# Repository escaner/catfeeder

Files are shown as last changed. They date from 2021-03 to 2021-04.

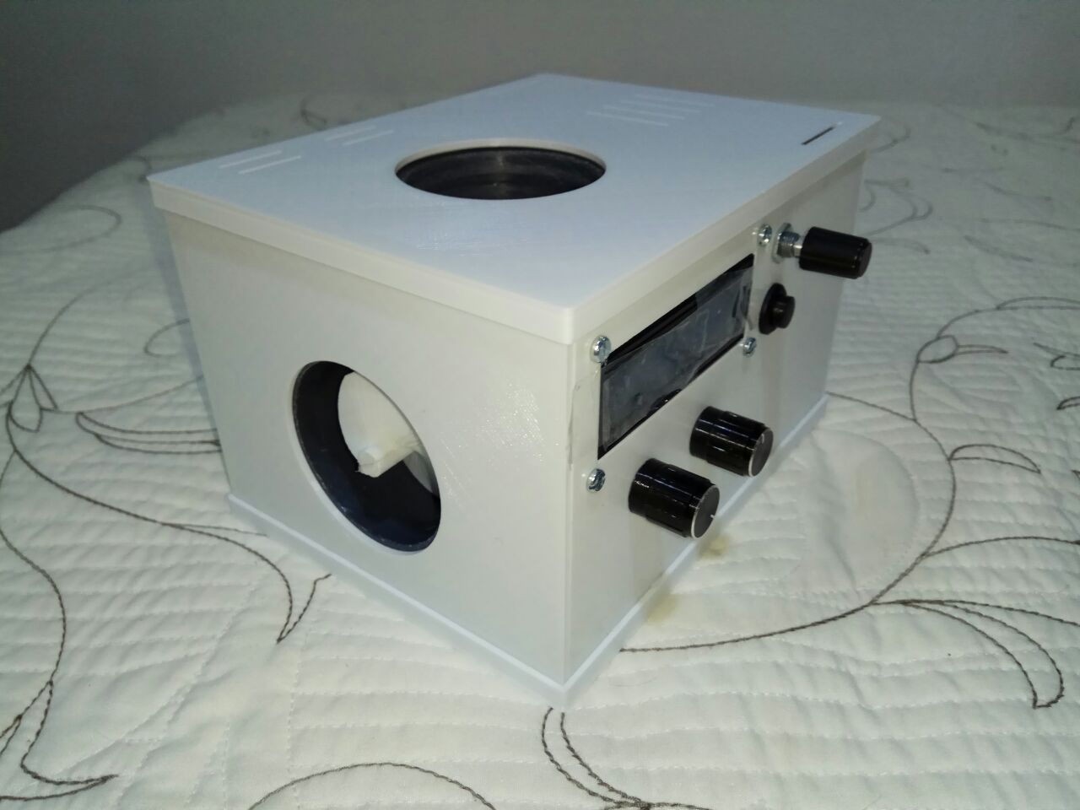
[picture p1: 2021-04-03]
doc/images/case2.jpg

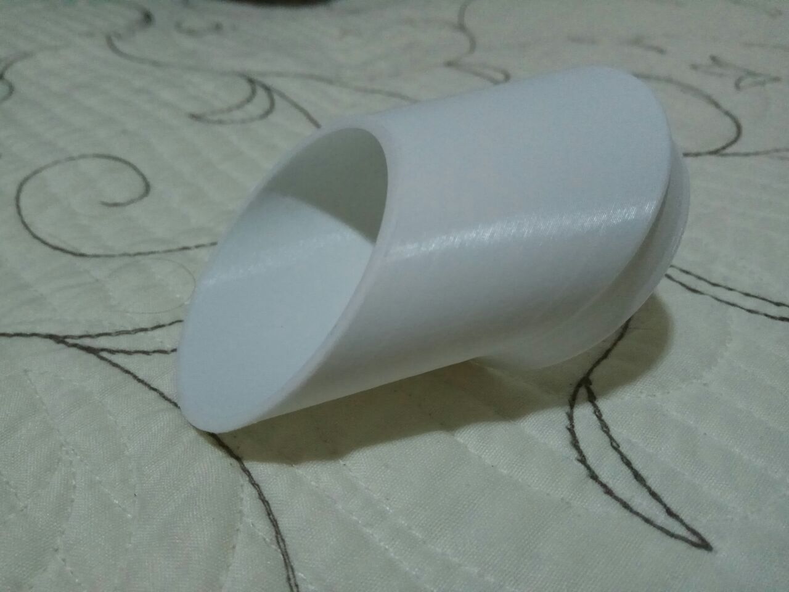
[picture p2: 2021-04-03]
doc/images/ramp1.jpg

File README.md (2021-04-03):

https://github.com/escaner/catfeeder

Catfeeder is an Arduino project to build am automatic cat feeder that
allows to program several feeding times so your mascot keeps getting food.

3D printed parts can be found here:
https://www.thingiverse.com/thing:4815584

The core of the system is an Arduino Nano or clone (small Arduino Uno
compatible) with a stepper motor connected to an auger, a display,
some buttons and a real time clock to keep the time in case the power
temporarily fails.

This is the list of electronic parts for the project:

* 1 x Arduino Nano compatible microcontroller
* 1 x SchmalzHaus EasyDriver: stepper motor controller
* 1 x Hanpose 17HS3430 stepper motor (12V)
* 1 x 1602 LCD display (without I2C module)
* 1 x Potentiometer 5 (or 10) KOhm for display brightness
* 1 x Potentiometer 10 KOhm for display contrast
* 1 x rotary encoder with pushbutton
* 1 x temporary pushbutton
* 1 x Robotdyn DS1307 I2C RTC module with battery as real time clock and backup
* 1 x Robotdyn LM2596 DC-DC Step-down Adjustable Power Supply Module (set
  to 5V output)
* 1 x DC barrel jack for 12V DC input required by the motor
* 1 x 12V 1.2A DC power supply (brick wall or as you prefer)

Note that in order for the reset function to correctly work, the Arduino Nano
needs to have the new Optiboot bootloader: the old one bugs out on reset
with the watchdog library.

More info can be found in the doc directory, including schematics and
pictures.

Other items used:
* 3D printer for case and parts
* Drill and 3mm bit to make hole in the T for the screw where the motor mount
  will lean
* PVC 50mm T pipe for water
* Epoxy two component glue (to fix T, bottom and front sides of case)
* Hot glue gun (to fix motor mount to T, left and right sides of case and
  also Arduino, motor controller and RTC to the case)
* M3 screws and nuts (to fix LCD, motor to its mount, auger to motor, screw in
  T and switched power supply)

Software features:
* Eight (can be increased up to 10) programmable feed times (including time,
  days of the week and quantity). Stored in the Arduino EEPROM (not lost on
  power off).
* Real Rime Clock with battery to keep time in case of power loss.
* Possibility of skipping next feed
* Time stored in UTC format for automatic DST changes (CET timezone
  programmed, can be easily changed in config.h).
* Day of the week is currently in Spanish, but not hard to change to English,
  code already prepared for that.
* Customizable through config.h and catfeeder.ino constants.
* Main display shows current date and time and also next feed day and time
* Manual feed function

This software needs my libraries REncoder and Switch:
https://github.com/escaner/REncoder
https://github.com/escaner/Switch

This project is based on Kitlaan and dodgey99 projects, seen here:
http://www.thingiverse.com/thing:27854
https://www.instructables.com/Automatic-Arduino-Powered-Pet-Feeder/

Copyright (C) 2020-2021, Óscar Laborda

This file is part of Catfeeder software.

Catfeeder is free software: you can redistribute it and/or modify
it under the terms of the GNU General Public License as published by
the Free Software Foundation, either version 3 of the License, or
(at your option) any later version.

Catfeeder is distributed in the hope that it will be useful,
but WITHOUT ANY WARRANTY; without even the implied warranty of
MERCHANTABILITY or FITNESS FOR A PARTICULAR PURPOSE.  See the
GNU General Public License for more details.

You should have received a copy of the GNU General Public License
along with Catfeeder.  If not, see <https://www.gnu.org/licenses/>.

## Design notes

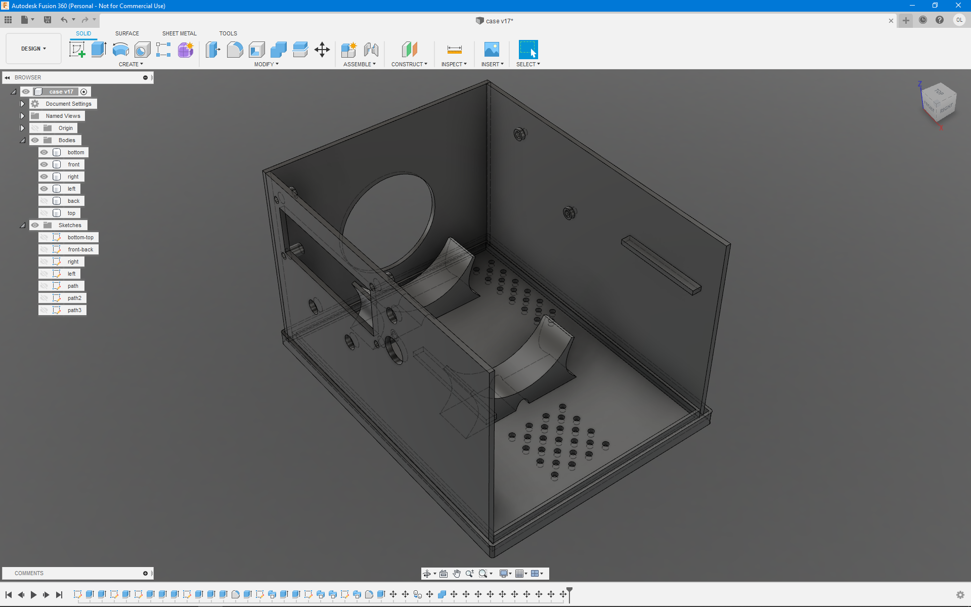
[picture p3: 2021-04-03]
doc/images/case6.png

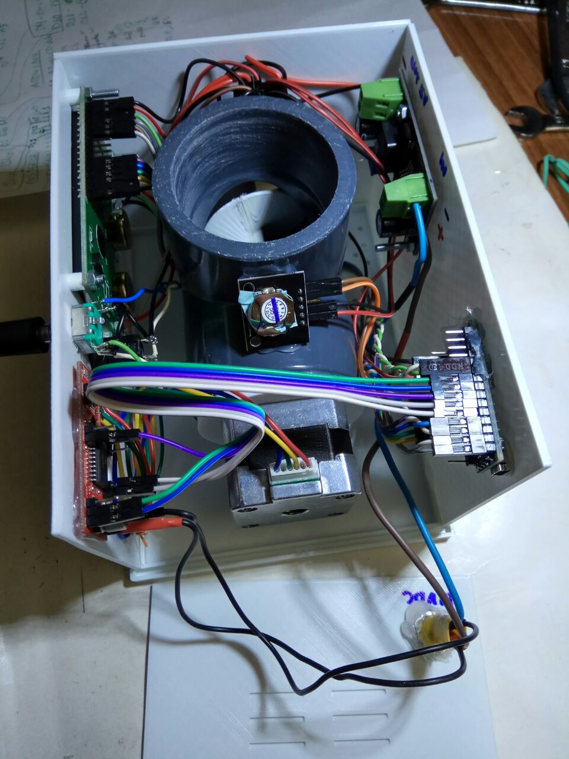
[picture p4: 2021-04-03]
doc/images/inside0.jpg

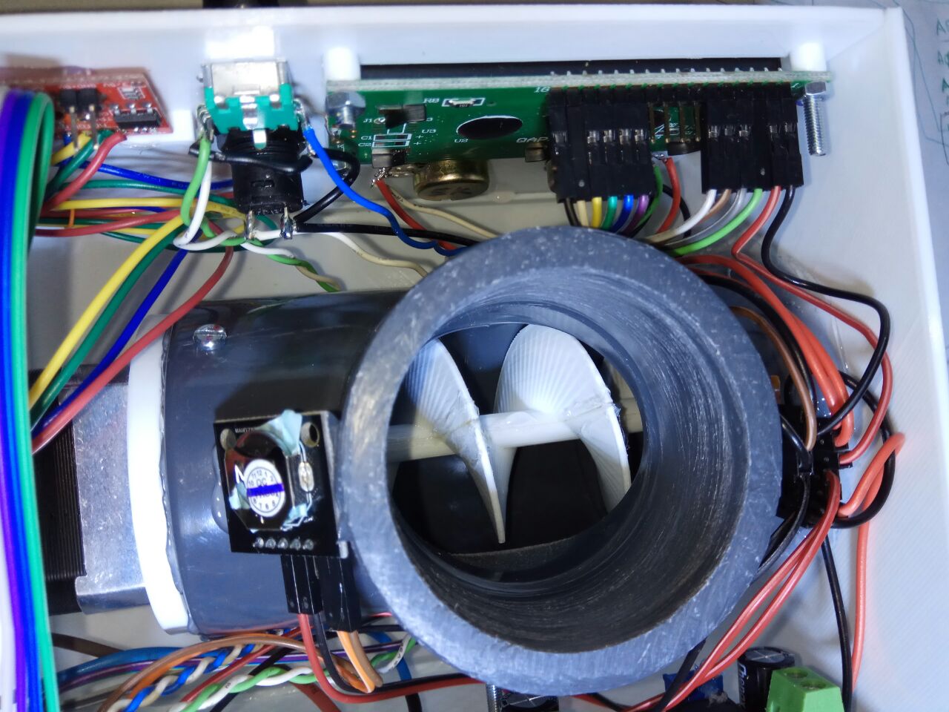
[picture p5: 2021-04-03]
doc/images/inside1.jpg

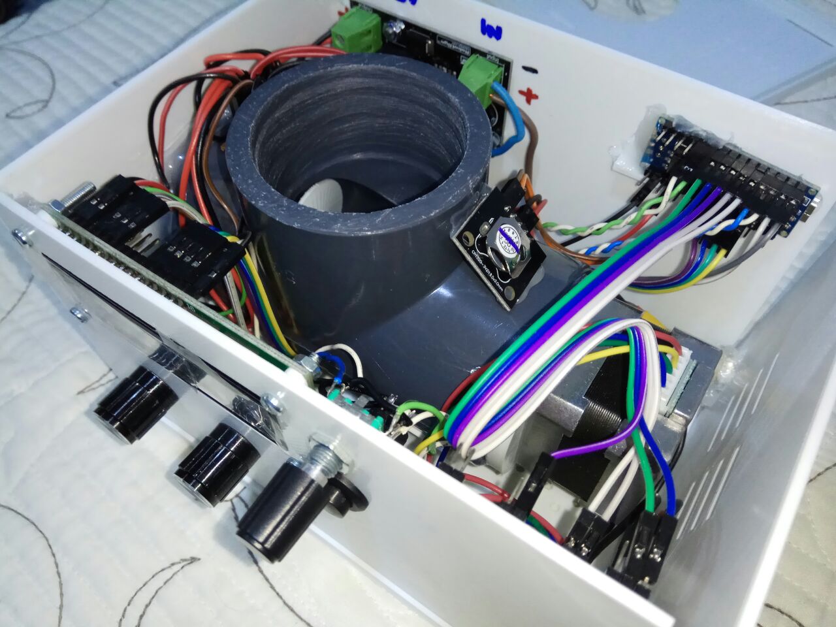
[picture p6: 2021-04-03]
doc/images/inside2.jpg

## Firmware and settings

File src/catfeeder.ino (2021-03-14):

#include "config.h"
#include <avr/wdt.h>
#include "event.h"
#include "action.h"
#include "feeds.h"
#include "switchpnl.h"
#include "clock.h"
#include "display.h"
#include "auger.h"


/*************/
/* Constants */
/*************/

// Swtich & encoder constants
static const uint8_t ENC_NUM_PINS = 2U;  // Number of pins per encoder
static const uint8_t NUM_BUTTONS = 2U;  // Number of swtiches of type button

// ARDUINO NANO connections
// Switches
static const uint8_t PIN_ENC[ENC_NUM_PINS] = { 2, 3 };
static const uint8_t PIN_BTN_ENT = 9;
static const uint8_t PIN_BTN_BCK = 10;
// Display
static const uint8_t PIN_LCD_RS = 12;
static const uint8_t PIN_LCD_E = 11;
static const uint8_t PIN_LCD_D4 = A3;
static const uint8_t PIN_LCD_D5 = A2;
static const uint8_t PIN_LCD_D6 = A1;
static const uint8_t PIN_LCD_D7 = A0;
// RTC
static const uint8_t PIN_RTC_SDA = A4;
static const uint8_t PIN_RTC_SCL = A5;
// EasyDriver with stepper motor
static const uint8_t PIN_ED_ENABLE = 8;
static const uint8_t PIN_ED_MS1 = 6;
static const uint8_t PIN_ED_MS2 = 7;
static const uint8_t PIN_ED_DIR = 5;
static const uint8_t PIN_ED_STEP = 4;


/*************/
/* Variables */
/*************/

// Object to control feeding times
static Feeds FeedData;

// Object to manage the input buttons and rotary encoder
static SwitchPnl SwitchPanel(PIN_ENC[0], PIN_ENC[1], PIN_BTN_ENT, PIN_BTN_BCK);

// Object to manage time and conversions
static Clock Rtc(TIMEZONE_DIFF, ENABLE_DST);

// Object to manage the LCD display
static Display Lcd(PIN_LCD_RS, PIN_LCD_E, PIN_LCD_D4, PIN_LCD_D5, PIN_LCD_D6,
  PIN_LCD_D7);

// Object to control the auger on the EasyDriver stepper motor
static Auger Edsm(PIN_ED_STEP, PIN_ED_DIR, PIN_ED_MS1, PIN_ED_MS2,
  PIN_ED_ENABLE, AUGER_RPM, AUGER_EIGHTH_REVS_PER_MEAL_QTY,
  AUGER_EIGHTH_REVS_BACKUP);


/***********/
/* Methods */
/***********/

// Local function prototypes
// Arduino generates incorrectly the ones using the Event class
static bool sendEventAndHandleActions(Event E);
static Event eventTime();
static Event eventNextMeal();
static bool checkFeedTime();
static void initClock();
static void reboot();


/*
 *   Arduino initialization function.
 */
void setup()
{
  // Initialize buttons object
  SwitchPanel.init();

  // Initialize RTC and check for errors
  initClock();

  // Initialize feed data structure
  FeedData.init(Rtc.getOfficial());

  // Send event to initialize display
  sendEventAndHandleActions(Event(Event::EvInit));
}


/*
 *   Arduino loop function.
 */
void loop()
{
  static unsigned long LastCheckFeed = 0UL;
  static unsigned long LastUpdateTime = 0UL;
  static unsigned long LastMealTime;
  static bool UpdateMealTime = false;
  unsigned long CurTime;

  // Get current time
  CurTime = millis();

  // Check update time (counter overflow works well)
  if (CurTime - LastUpdateTime >= TIME_UPDATE_INTERVAL)
  {
    LastUpdateTime = CurTime;
    sendEventAndHandleActions(eventTime());
  }

  // Check feed time every FEED_CHECK_INTERVAL ms (counter overflow works well)
  if (CurTime - LastCheckFeed >= FEED_CHECK_INTERVAL)
  {
    LastCheckFeed = CurTime;
    if (checkFeedTime())
    {
      LastMealTime = CurTime;
      UpdateMealTime = true;
    }
  }

  // MEAL_UPDATE_DELAY ms after serving a meal, the LCD next meal is updated
  if (UpdateMealTime && CurTime - LastMealTime >= MEAL_UPDATE_DELAY)
  {
    UpdateMealTime = false;
    sendEventAndHandleActions(eventNextMeal());
  }

  // Loop checking switch panel
  for (uint16_t SwIdx=SWITCH_LOOP_CNT; SwIdx; SwIdx--)
  {
    Event::SwitchEvent SwE;
    bool ManuallyFeeding = false;

    // Loop for manual feeding (synchronous interactive task)
    do
    {
      // Did we get a switch event?
      if ((SwE = SwitchPanel.check(SWITCH_STAB_LOOP_CNT)) != Event::SwEvNone)
      {
       // Build event
        Event E(Event::EvSwitch);
        E.Switch = SwE;

        // Notify event and handle unchained actions
        ManuallyFeeding = sendEventAndHandleActions(E);
      }
      else if (ManuallyFeeding)
        // Keep feeding when no switches registered
        Edsm.keepFeeding();
    }
    while (ManuallyFeeding);
  }
}


/*
 *   Prepares an event to update the time in the LCD.
 */
static Event eventTime()
{
  // Create an event that contains the official time from the RTC
  Event E(Event::EvTime);
  E.Time = Rtc.getOfficial();

  // Return the event
  return E;
}


/*
 *   Prepares an event to update LCD display next meal info
 */
static Event eventNextMeal()
{
  // Create event to update the next meal in the LCD 
  Event E(Event::EvNextMeal);
  E.NextMeal.Status = FeedData.timeOfNext(&E.NextMeal.Dotw, &E.NextMeal.Hour,
    &E.NextMeal.Minute);

  // Return the event
  return E;
}


/*
 *   Sends an event E to the LCD display and handles actions unchained by it.
 *  Parameters:
 *  * E: event to send to the LCD display
 *  Returns:
 *  * false: we are not manually feeding
 *  * true: we are manually feeding
 */
static bool sendEventAndHandleActions(Event E)
{
  bool End = false;
  bool Feeding = false;
  Action A;

  // Loop until no more actions requested or no more events needed
  do
  {
    // Send event and record new requested action
    A = Lcd.event(E);
  
    // Check the requested action, perform it and prepare new event when needed
    switch (A.Id)
    {
    case Action::AcNone:
      End = true;
      break;
    case Action::AcNeedTime:
      E = eventTime();
      break;
    case Action::AcNeedNextMeal:
      E = eventNextMeal();
      break;
    case Action::AcNeedTimeUtc:
      E.Id = Event::EvTimeUtc;
      E.Time = Rtc.getUtc();
      break;
    case Action::AcNeedMeal:
      E.Id = Event::EvMeal;
      E.pMeal = FeedData.getMeal(A.MealId);
      break;
    case Action::AcSetTimeUtc:
      Rtc.setUtc(A.Time);
      FeedData.reset(Rtc.getOfficial());  // Reset skip & calculate next meal
      End = true;
      break;
    case Action::AcSetMeal:
      FeedData.saveMeal(A.MealId);        // Save meal data to EEPROM
      FeedData.reset(Rtc.getOfficial());  // Reset skip & calculate next meal
      End = true;
      break;
    case Action::AcManualFeedStart:
      Edsm.startFeeding();
      Feeding = true;
      End = true;
      break;
    case Action::AcManualFeedContinue:
      // No Edsm feeding here, it is handled by the caller
      Feeding = true;
      End = true;
      break;
    case Action::AcManualFeedEnd:
      Edsm.endFeeding();
      // Feeding = false;
      End = true;
      break;
    case Action::AcSkipMeal:
      if (FeedData.isSkippingNext())
        FeedData.unskipNext();
      else
        FeedData.skipNext();
      End = true;
      break;
    case Action::AcReset:
      FeedData.resetEeprom();  // Invalidate meal data in EEPROM
      reboot();                // Reboot the Arduino
      End = true;
      break;
    }
  } while (!End);

  // Return whether we are manually feeding
  return Feeding;
}


/*
 *   Checks whether it is time for a meal, serves it and updates the
 *  next meal in the FeedData object and LCD.
 *  Returns:
 *  * true: when a meal is served next meal needs to be updated in the LCD
 *    in a minute at lease.
 *  * false: no meal was served, no further updates required.
 */
static bool checkFeedTime()
{
  int8_t Quantity;
  bool MealServed = false;

  // Get current official time from the RTC and check whether it is meal time
  Quantity = FeedData.check(Rtc.getOfficial());

  // It is meal time when the quantity is not 0
  if (Quantity)
  {
    // Positive quantity is meal amount, negative when we are skipping the meal
    if (Quantity > 0)
      // Deliver meal
      Edsm.feed(Quantity);

    // Update LCD
    sendEventAndHandleActions(eventNextMeal());

    // Both when served and skipped, signal to update display later
    MealServed = true;
  }

  return MealServed;
}


/*
 *   Initializes the Real Time Clock and checks for errors.
 *  Assumes that the LCD has been initialized.
 */
static void initClock()
{
  // Initialize RTC and check for error
  if (Rtc.init())
  {
    Lcd.error(F("Rtc.init()"));
    abort();
  }

  // Check if the clock is ticking
  if (!Rtc.isrunning())
  {
    // If not running, start the clock by setting a random time
    Rtc.setUtc(DateTime());

    // Check again
    if (!Rtc.isrunning())
    {
      Lcd.error(F("Rtc.isrunning()"));
      abort();
    }
  }
}


/*
 *   Reboots the Arduino by triggering the watchdog.
 */
static void reboot()
{
  // Clear display and show message
  Lcd.resetMessage();

  // Enable watchdog to 2s
  wdt_enable(WDTO_2S);

  // Loop forever so watchdog engages and resets
  for (;;)
  {
    // Display animation while waiting the reboot
    Lcd.resetAnimation();
    delay(300);
  }
}

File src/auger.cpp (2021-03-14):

#include "config.h"
#include <assert.h>
#include "auger.h"


/*
 *   Constructor. Initializes class and stepper motor EasyDriver controller.
 *  Parameters:
 *  * PinStep: STEP pin in controller, marking the steps of the motor.
 *  * PinDir: DIR pin in controller, determining direction of the movement.
 *  * PinMs1: MS1 pin in controller, determining step size with MS2.
 *  * PinMs2: MS2 pin in controller, determining step size with MS1.
 *  * PinEnable: ENABLE pin in controller, activating enery to the motor.
 *  * Rpm: movement speed in revolutions per second. MAX=120.
 *  * EighthRevsPerQtyUnit: Eighth revolutions per quantity unit. One full
 *    revolution is 8 eighths. Note that Quantity*EighthRevsPerQtyUnit<256
 *    or an overflow condition will happen.
 */
Auger::Auger(uint8_t PinStep, uint8_t PinDir, uint8_t PinMs1, uint8_t PinMs2,
    uint8_t PinEnable, uint8_t Rpm, uint8_t EighthRevsPerQtyUnit,
    uint8_t EighthRevsPerBackup):
  _PinStep(PinStep),
  _PinDir(PinDir),
  _PinMs1(PinMs1),
  _PinMs2(PinMs2),
  _PinEnable(PinEnable),
  _EighthRevsPerQtyUnit(EighthRevsPerQtyUnit),
  _StepsContinuousFeed(EighthRevsPerQtyUnit * _STEPS_PER_8REV),
  _StepsBackup(EighthRevsPerBackup * _STEPS_PER_8REV),
  // Calculate ms per half step
  _HalfStepTime( (unsigned int)
    ((60UL * 1000000UL) /
    (uint32_t(Rpm) * uint32_t(_STEPS_PER_REV * 2U))))
{
  // Avoid burning the motor!
  assert(Rpm <= 120U);

  // Prepare Arduino to control EasyDriver
  pinMode(PinStep, OUTPUT);
  pinMode(PinDir, OUTPUT);
  pinMode(PinMs1, OUTPUT);
  pinMode(PinMs2, OUTPUT);
  pinMode(PinEnable, OUTPUT);

  // Prepare EasyDriver controller
  digitalWrite(PinEnable, HIGH);
  digitalWrite(PinStep, LOW);
  digitalWrite(PinDir, _DIR_FORWARD);
  digitalWrite(PinMs1, HIGH);
  digitalWrite(PinMs2, HIGH);
}


/*
 *   Synchronously moves the auger to feed.
 *  Paramters:
 *  * Quantity: size of the meal. Note that Quantity*Hrqu<256
 *    or an overflow condition will happen.
 */
void Auger::feed(uint8_t Quantity) const
{
  uint16_t Steps;
  
  // Calculate number of steps for this meal
  Steps = uint16_t(_EighthRevsPerQtyUnit) * _STEPS_PER_8REV;
  //  Steps = uint16_t(Quantity * _EighthRevsPerQtyUnit) * _STEPS_PER_8REV;


  // Engage the motor
  _enableMotor();

  // Deliver the food turning the motor and jiggling every quantity unit
  while (Quantity--)
  {
    _jiggle();
    _turnMotor(Steps);
  }
 
  // Save power
  _disableMotor();
}


/*
 *   Starts a semi-synchronous feed.
 */
void Auger::startFeeding() const
{
  _enableMotor();
  keepFeeding();
}


/*
 *   Continues a semi-synchronous feed, jiggling on each call
 */
void Auger::keepFeeding() const
{
  _jiggle();
  _turnMotor(_StepsContinuousFeed);
}


/*
 *   Ends a semi-synchronous feed. Does not deliver actual food.
 */
void Auger::endFeeding() const
{
  _disableMotor();
}


/*
 *   Powers up the motor.
 */
void Auger::_enableMotor() const
{
  digitalWrite(_PinEnable, LOW);
}


/*
 *   Powers down the motor.
 */
void Auger::_disableMotor() const
{
  digitalWrite(_PinEnable, HIGH);
}


/*
 *   Turns the motor (auger)
 *   Parameters:
 *   * NumSteps: how many steps the motor will be turned
 */
void Auger::_turnMotor(uint16_t NumSteps) const
{
  while (--NumSteps)
  {
    // Perform one full step
    digitalWrite(_PinStep, HIGH);
    delayMicroseconds(_HalfStepTime);
    digitalWrite(_PinStep, LOW);
    delayMicroseconds(_HalfStepTime);
  }
}


/*
 *  Jiggles the auger back and forth to prevent it getting stuck.
 */
void Auger::_jiggle() const
{
  digitalWrite(_PinDir, _DIR_BACKWARD);
  _turnMotor(_StepsBackup);
  digitalWrite(_PinDir, _DIR_FORWARD);
  _turnMotor(_StepsBackup);
}

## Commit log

2020-11-22 Added switchpnl class
2020-11-27 Switchpnl updated with press and release events
2020-12-01 Added timer1 module
2020-12-12 Fixed next meal calculation
    [catfeeder.ino]
2020-12-12 Fixed next meal refresh after serving
    [catfeeder.ino]
2020-12-12 Update display after skip meal
    [catfeeder.ino]
2021-03-14 * Jiggle motor to avoid getting stuck * Added copy operators for Event and Action classes * Fixed manual feed stop delay * Improved event handling while manual feeding * Enabled micro-stepping x8
    [auger.cpp, catfeeder.ino, switchpnl.cpp]
2021-04-03 Added documentation
    [cat-feeder.fzz]
